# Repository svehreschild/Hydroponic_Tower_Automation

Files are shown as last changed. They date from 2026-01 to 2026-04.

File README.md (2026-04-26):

# Hydroponic_Tower_Automation
Hier finden Sie eine detaillierte Anleitung, um einen modularen Hydroponikturm zu automatisieren. Die Anleitung enthält einen Schaltplan, den Code der Software, eine Liste der benötigten Materialien und eine Schritt-für-Schritt-Anleitung.

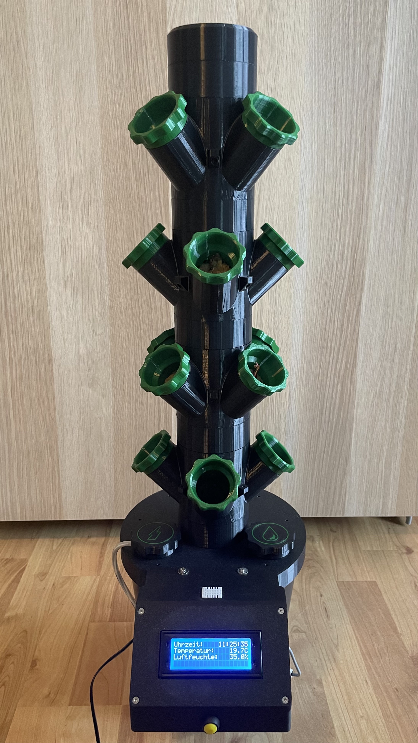
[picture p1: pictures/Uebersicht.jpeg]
Bild-Übersicht


## 3D-Druck
**Grundaufbau:** 
Zunächst werden die benötigten, modularen Komponenten für den Hydroponikturm mit einem 3D-Drucker gedruckt. Als Basis für unser Projekt haben wir die Designs von Luitzor verwendet, die unter der folgenden URL verfügbar sind: [Luitzor's Hydroponic Tower Designs](https://www.thingiverse.com/thing:5712775). Wir empfehlen, diese Designs als Ausgangspunkt zu verwenden, da sie bereits sehr gut durchdacht, modular und funktional erweiterbar sind.

Wir haben die Designs auf 75 % der Originalgröße skaliert, da wir in unserem Fall einen kleineren Turm automatisieren wollten, der auch auf einem Schreibtisch, einer Fensterbank oder ähnlichen begrenzten Flächen Platz findet. Damit das Druckergebnis optimal wird, empfehlen wir die folgenden Druckeinstellungen:

- Material: Extrudr PET-G (lebensmittelecht)
- Drucker: Bambu Lab X1C 
- 0.16mm Optimal @BBL X1C mit folgenden Anpassungen:
    - Fülldichte: 25 % (Gyroid)

Mindestens sollten die folgenden Komponenten gedruckt werden:
- 1x 4-Way_Planting_Module_Hollow_Twist.STL
- 4x Standard_Pot_02_For_4-5-Way_Planting_Module.STL
- 1x Module_Spacer_40mm.STL
- 1x Dispenser_Module_Internal.STL
- 1x IKEA_Muskot_24cm_Lid.STL
- 1x Lid_Without_Holes.STL
- 1x Pump_Cap.STL
- 1x Pump_Cap_Symbol.STL
- 1x Filling_Cap.STL
- 1x Filling_Cap_Symbol.STL

Soll der Turm mehrere Ebenen haben, müssten Sie pro Ebene einmal `4-Way_Planting_Module_Hollow_Twist.STL`, viermal `Standard_Pot_02_For_4-5-Way_Planting_Module.STL` und einmal `Module_Spacer_40mm.STL` drucken. Der Abstandhalter `Module_Spacer_40mm.STL` ist nicht zwingend notwendig, aber wir empfehlen ihn, um den Pflanzen mehr Platz zum Wachsen zu geben. Außerdem empfehlen wir, mehrere Pflanzenpods `Standard_Pot_02_For_4-5-Way_Planting_Module.STL`, als Reserve zu drucken, falls eine Pflanze nicht gedeiht oder ersetzt werden muss.

Bei der Kombination der Abdeckkappen und der zugehörigen Symbole empfehlen wir, die Symbole mit einem Kleber auf die Kappen zu kleben oder, mit einem Drucker, der über ein AMS (Automatisches Materialwechselsystem) verfügt, die Symbole in einer anderen Farbe zu drucken, um eine bessere Sichtbarkeit zu gewährleisten.

Gedruckte Symbole in Abdeckkappen

**Unsere 3D Files**:
Zur sicheren Unterbringung der Elektronik, haben wir ein Gehäuse und Platinenhalterungen designed. Diese Dateien finden Sie im Ordner `3D_Designs`. Sie benötigen die folgenden Dateien jeweils einmal:
- Vertical_Gardening_Housing.stl
- Vertical_Gardening_Housing_Lid.stl
- Sockelhalter_Platine_Main.stl
- Sockelhalter_Relais.stl

**Kalkulation:** 
In der Datei `3D_Berechnung.xlsx` können Sie vorab kalkulieren, wie viel Filament für den Druck der benötigten Komponenten in Abhängigkeit zur Anzahl der Etagen und zu den empfohlenen Einstellungen gebraucht wird.

**Informationen zum Filament:**
Bei dem verwendeten Filament handelt es sich um lebensmittelechtes PET-G von Extrudr. Weitere Informationen zum Filament finden Sie hier in dem `Regulatorischen Datenblatt`: [Extrudr PET-G](https://www.extrudr.com/de/de/products/petg/).

Es sei noch darauf hingewiesen, dass PET-G im Vergleich zu PLA eine höhere Drucktemperatur benötigt und die Druckbetttemperatur ebenfalls höher eingestellt werden muss.

Anstelle des PET-G der Firma Extrudr kann auch anderes, lebensmittelechtes PET-G Filament verwendet werden. Es sollte jedoch auf entsprechende Zertifikate und Angaben des Herstellers geachtet werden, um sicherzustellen, dass das Filament für den Kontakt mit Lebensmitteln geeignet ist. 

Falls Sie sich mit dem Thema lebensmittelechtes Filament näher beschäftigen möchten, finden Sie hier einige weitere Informationen: 
- [Leitfaden für den lebensmittelechten 3D-Druck](https://formlabs.com/de/blog/leitfaden-lebensmittelechtheit-3d-druck/)
- [FDA-Bestimmungen, CFR 21](https://www.accessdata.fda.gov/scripts/cdrh/cfdocs/cfcfr/CFRSearch.cfm)
- [EU-Richtlinien 10/2011](https://eur-lex.europa.eu/legal-content/EN/ALL/?uri=CELEX%3A32011R0010)

## Elektronik
Die Automatisierung des Hydroponikturms umfasst die Erstellung einer Steuerplatine, die folgende Komponenten beinhaltet:

- Arduino Nano
- Display mit I2C Schnittstelle
- DHT22 Sensor (für Temperatur und Luftfeuchtigkeit)
- Schwimmerschalter (Wasserstandserkennung)
- Buck-Converter
- Relaismodul
- Pumpe
- RTC Modul

Eine detaillierte Stückliste mit Vorschlägen zu Anbietern ist in der Datei `Bauteilliste.xlsx` enthalten.

In der Bauteilliste ist auch eine Blanko-Platine aufgeführt. Wir haben im Rahmen unseres Projektes eine Lochrasterplatine entworfen, auf der die benötigten Komponenten verlötet wurden. Es steht Ihnen jedoch frei, ob Sie eine eigene Platine entwerfen oder eine Lochrasterplatine verwenden möchten.

Wir empfehlen die Erstellung einer Platine mit den Maßen (120 mm, 40 mm) um diese optimal in die vorgesehene 3D-gedruckte Halterung einzusetzen.

Sie benötigen außerdem noch folgendes Zubehör:
- Lötstation
- Lötzinn
- Schrumpfschlauch
- Kabelbinder
- Kabel

Anhand des [Schaltplans](Schaltplan.pdf) können Sie die Verdrahtung der einzelnen Komponenten nachvollziehen:
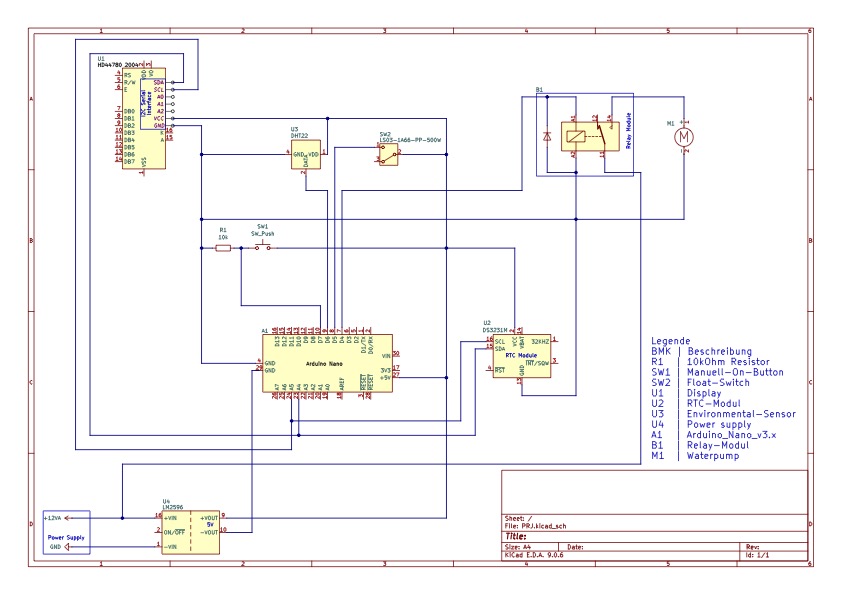
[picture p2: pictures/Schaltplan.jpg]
Schaltplan


## Zusätzliches Zubehör
Um dem Hydroponikturm eine stabile und wasserdichte Basis zu geben, empfehlen wir die Verwendung eines passenden Topfs. In unserem Fall haben wir (anders als im Originaldesign von Luitzor) einen entsprechenden Topf im Baumarkt mit einem Außendurchmesser von 21,5cm gekauft, der sich mit einem gekauften Dichtungsband für Fenster und Türen, welches in den Deckel eingeklebt wird, abdichten lässt.
Der (auf 75% skalierte) Deckel hat einen Innendurchmesser von ca. 22cm, daher sollte der Topf einen Außendurchmesser haben, der etwas kleiner ist, damit der Deckel passt.

Deckel

## Software
Der Quellcode für die Steuerung des Hydroponikturms ist in der Datei `Hydroponic_Tower_Automation.ino` enthalten. 

Die Software ist so konzipiert, dass sie die folgenden Funktionen erfüllt:
- Speicherung und Abruf von Einstellungen über das RTC-Modul
- Anzeige von Temperatur, Luftfeuchtigkeit und Systemstatus auf dem Display
- Displayanzeige der verbleibenden Laufzeit der Pumpe oder der restliche Pausenzeit
- Pausenfunktion: Durch Drücken des Tasters für 3 Sekunden wird eine 3-stündige Bewässerungspause aktiviert. Ein kurzer Druck während der Pause bricht diese vorzeitig ab
- Steuerung der Pumpe basierend auf manuellen Eingaben und voreingestellten Zeitintervallen
- Alarmierung bei zu niedrigem Wasserstand und Verhindern des Pumpenbetriebs in diesem Fall

Sollten Sie andere Zeitintervalle, Bewässerungsdauern oder zusätzliche Funktionen benötigen, können Sie den Quellcode entsprechend anpassen.

Damit der Code kompiliert werden kann, benötigen Sie die folgenden Bibliotheken, die Sie über den Bibliotheksverwalter der Arduino IDE installieren können:
- RTClib von Adafruit (bei uns Version 2.1.4)
- LiquidCrystal_I2C von Martin Kubovčík, Frank de Brabander (bei uns Version 2.0.0)
- DHT sensor library von Adafruit (bei uns Version 1.4.6)

Spielen Sie den Code auf Ihren Arduino Nano, während Sie die Verdrahtung mit dem RTC-Modul gemäß dem Schaltplan verbunden haben, um die Uhrzeit einmalig einzustellen. Nach dem Schreiben der aktuellen Uhrzeit auf das RTC-Modul können Sie diesen Codeblock erneut auskommentieren, um die Uhrzeit nicht bei jedem Neustart zu überschreiben. Sobald die Uhrzeit eingestellt ist, ist das RTC-Modul in der Lage, die Zeit auch bei einem Stromausfall (der Hauptspannungsversorgung) zu behalten, da es über eine Knopfzellenbatterie weiterhin versorgt wird.

## Montage
Beginnen Sie mit dem Zusammenbau der 3D-gedruckten Komponenten gemäß der Anleitung von [Luitzor](https://www.thingiverse.com/thing:5712775). Dies sollte sehr intuitiv sein. 

Bauen Sie jeweils eine Baugruppe aus einem 4-Wege-Pflanzenmodul, vier Pflanzenpods und einem Abstandhalter zusammen. Wiederholen Sie diesen Schritt für die gewünschte Anzahl an Etagen. Nun beginnen Sie mit dem Dispenser-Modul, an das nun der Wasserschlauch angeschlossen wird.

Foto Dispenser-Modul mit Schlauch

Im Anschluss nehmen Sie die zuvor erstellten Baugruppen und stapeln diese auf das Dispenser-Modul. Der Wasserschlauch wird durch die runden Ausschnitte in allen Modulen hindurchgeführt.  

Modulgruppe mit Schlauch1

Modulgruppe mit Schlauch2

Achten Sie darauf, dass die Module korrekt ausgerichtet sind, damit die Pflanzenpods später nicht direkt untereinander, sondern um 45 Grad versetzt, eingesetzt werden können.

Modulgruppen um 45 Grad versetzt

Der Deckel des Topfs wird ebenfalls bestückt mit den Abdeckungen für die Pumpe und dem Zugang zum Wassertank. In der Mitte des Deckels wird der Turm aufgeschraubt.

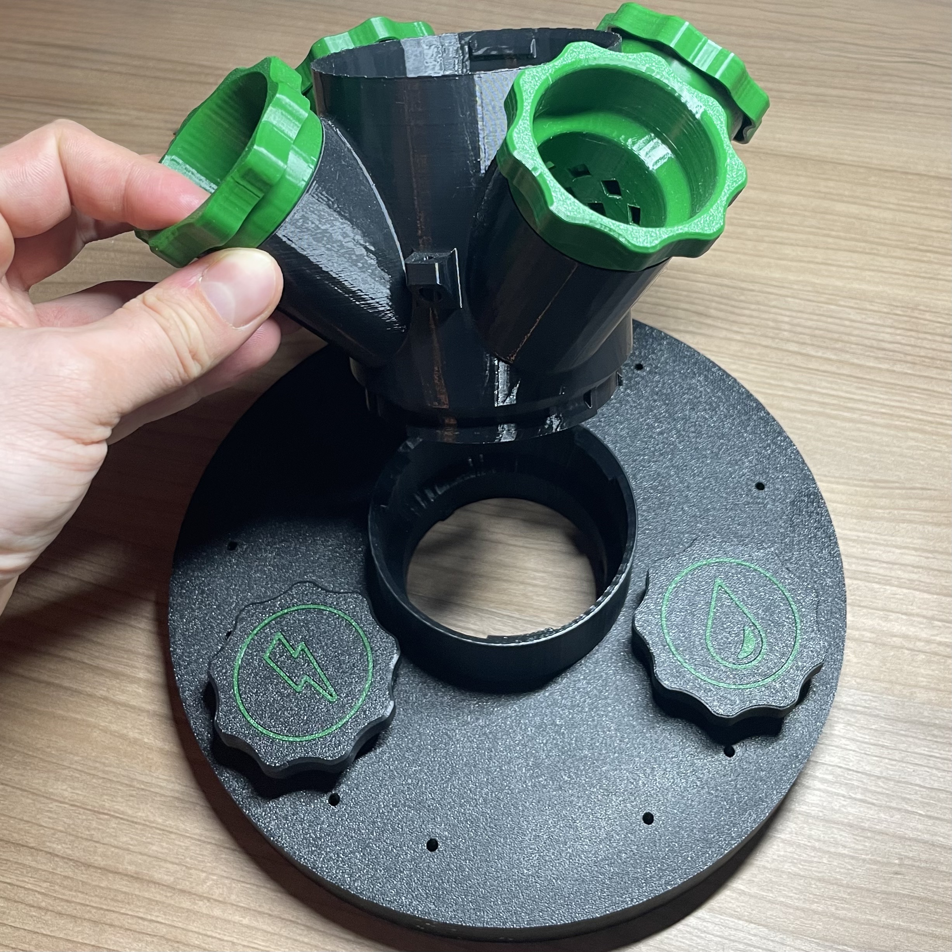
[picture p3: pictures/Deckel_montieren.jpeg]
Bestückung des Deckels


In den Topf wird ein entsprechendes Loch für den Schwimmerschalter gebohrt, der dann von außen in den Topf eingesetzt und mit einer Mutter befestigt wird. Achten Sie darauf, dass der Sensor wasserdicht im Topf sitzt, damit kein Wasser austreten kann.

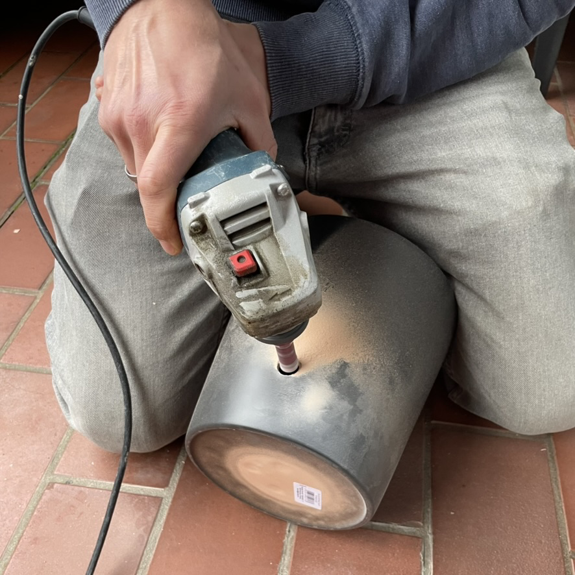
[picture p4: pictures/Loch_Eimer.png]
Loch im Topf


Anschließend erhitzen Sie vier M3 Einschmelzgewinde (mit einer Länge von ca. 6 mm) und setzen diese in das Gehäuse zur Befestigung des Deckels ein.

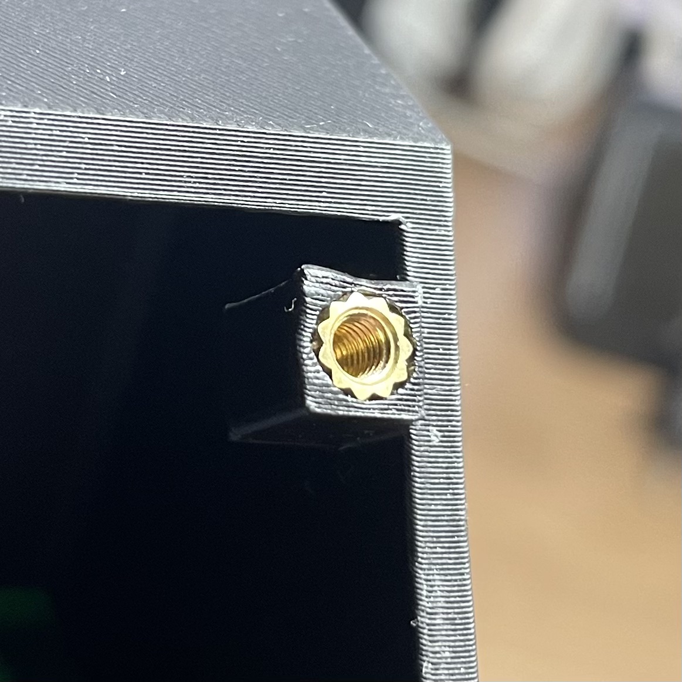
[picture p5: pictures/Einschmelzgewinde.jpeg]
Einschmelzgewinde


Außerdem verkleben Sie die Hauptplatinenhalterung und den DHT22 im Gehäuse mit einem geeigneten Kleber (z. B. Zweikomponentenkleber).
Achten Sie darauf, die Platinenhalterung so zu positionieren, dass der Anschluss für die Spannungsversorgung der Platine durch die Aussparung im Gehäuse passt.

Die Platinenhalterung für das Relaismodul wird lediglich mit zwei M2,5 Schrauben (Länge maximal 4,5 mm) befestigt. Das RTC-Modul wird in dem Gehäuse an dem dafür vorgesehenen Platz mit drei M2,5 Schrauben (Länge maximal 6 mm) angebracht. 
Beachten Sie, dass zu lange Schrauben das Gehäuse beschädigen können.
Den Taster zum Aktivieren des manuellen Pumpenbetriebs können Sie an der Vorderseite des Gehäuses in dem entsprechenden Ausschnitt anbringen und ihn mit der mitgelieferten Mutter befestigen.

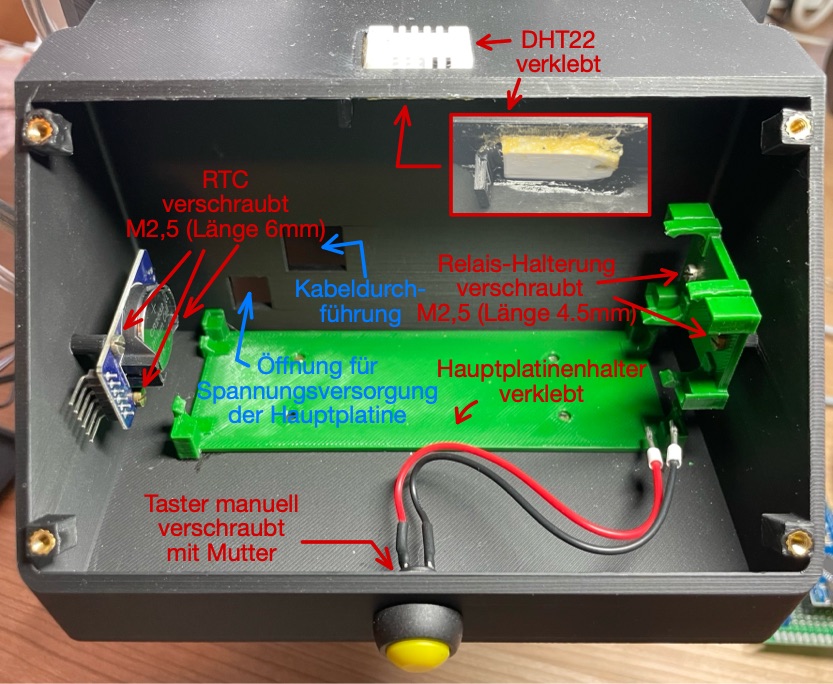
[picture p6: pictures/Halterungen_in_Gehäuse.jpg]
Gehäuse mit Komponenten und Beschriftungen


In den Deckel des Gehäuses wird das Display mit vier M2,5 Schrauben (Länge maximal 4,5 mm) befestigt.
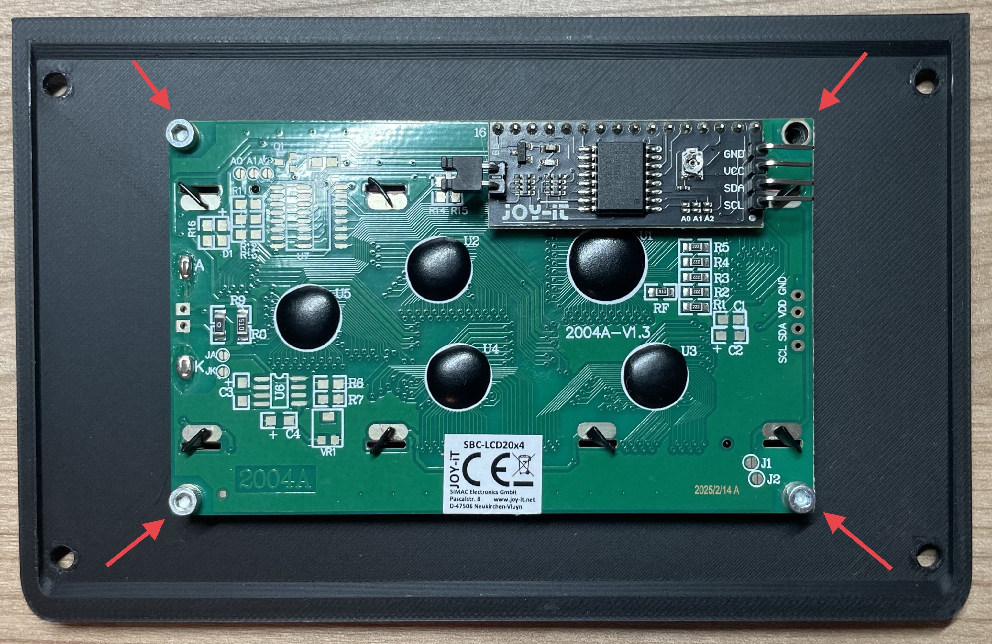
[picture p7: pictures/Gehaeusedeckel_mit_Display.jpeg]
Gehäusedeckel mit Display


Im Anschluss verlöten Sie die Elektronikkomponenten, die auf der Hautplatine Platz finden sollen gemäß dem [Schaltplan](Schaltplan.pdf).
Sinnvoll ist es die Verbindungen zu den einzelnen externen Komponenten über Schraubverbindungen herzustellen, damit diese bei Bedarf einfach getauscht werden können. 

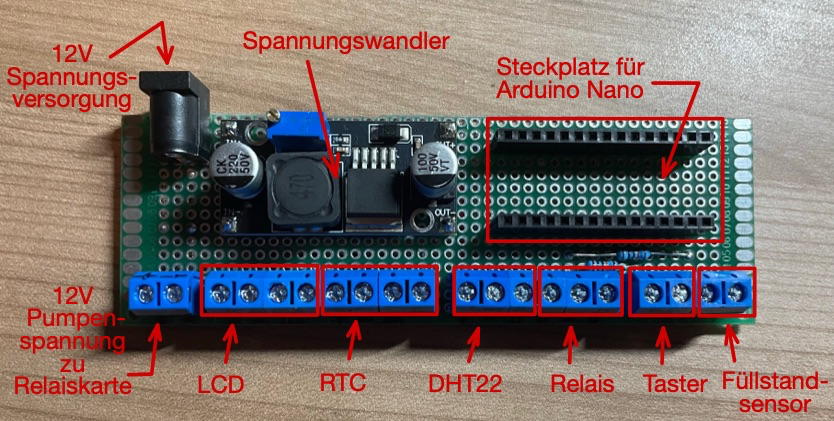
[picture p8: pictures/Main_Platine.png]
Hauptplatine


Die Verkabelung der einzelnen Komponenten im Gehäuse erfolgt ebenfalls gemäß dem [Schaltplan](Schaltplan.pdf). Achten Sie darauf, dass die Kabel ausreichend lang sind, um alle Komponenten zu erreichen. Sinnvoll ist es, die Kabel mit Schrumpfschlauch zu isolieren und entsprechende Aderendhülsen zu verwenden.

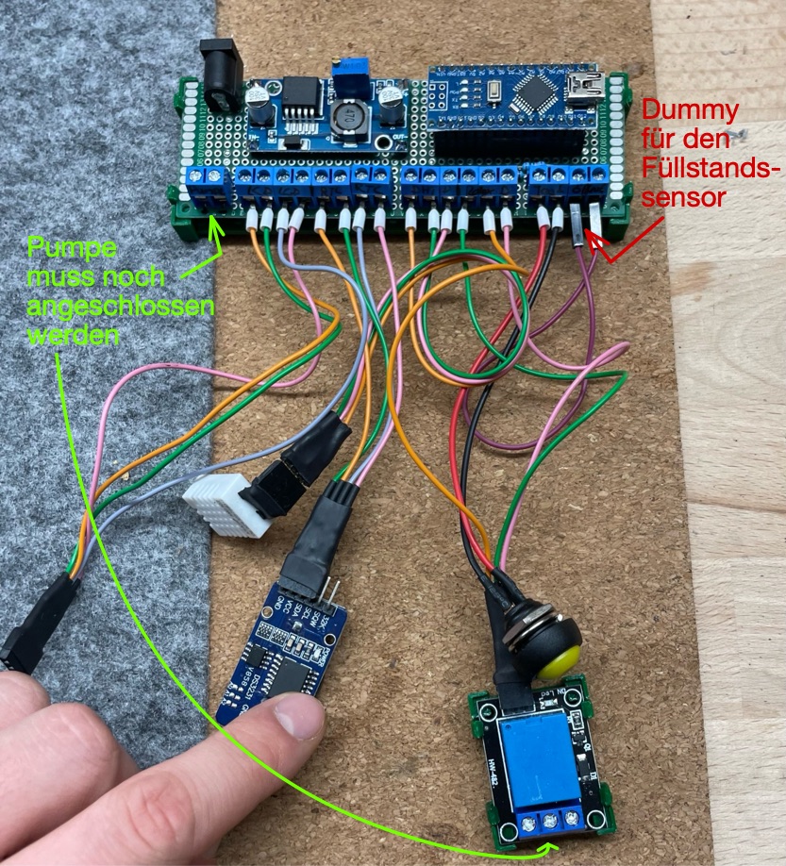
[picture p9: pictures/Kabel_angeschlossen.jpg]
Hauptplatine mit Verkabelung


Bevor die Pumpe in den Topf eingesetzt wird, wird sie mit einem Stück Fliegengitter vor Verunreinigungen geschützt. Das Fliegengitter wird mit einem Kabelbinder an der Pumpe befestigt. 

Pumpe mit Fliegengitter

Anschließend wird die Pumpe durch den dafür vorgesehenen Ausschnitt im Deckel des Topfs eingesetzt und mit der Platine entsprechend des Schaltplans verbunden. Das Kabel der Pumpe sollte durch die Aussparung an der Rückseite des Gehäuses geführt werden, damit dieses später geschlossen werden kann.

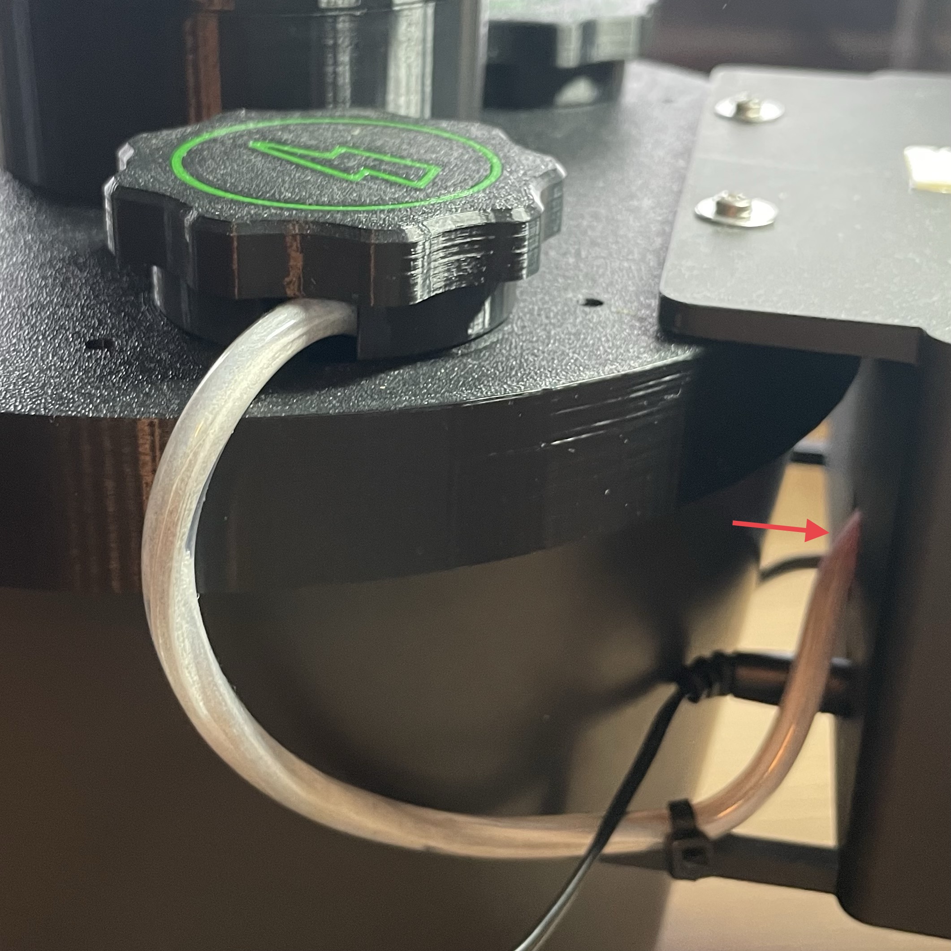
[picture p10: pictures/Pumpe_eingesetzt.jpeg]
Pumpe eingesetzt


Im Anschluss wird nun der finale Feinschliff der Verkabelung durchgeführt. Die Kabel sollten so verlegt werden, dass sie nicht im Weg sind und anschließend vorsichtig mit Kabelbindern fixiert und gebündelt werden. 
Sie können überschüssige Kabellängen kürzen oder aufrollen, um eine ordentliche Verkabelung zu gewährleisten.
Achten Sie darauf, dass Sie keine Kabel quetschen, wenn Sie die Kabelbinder fest ziehen.

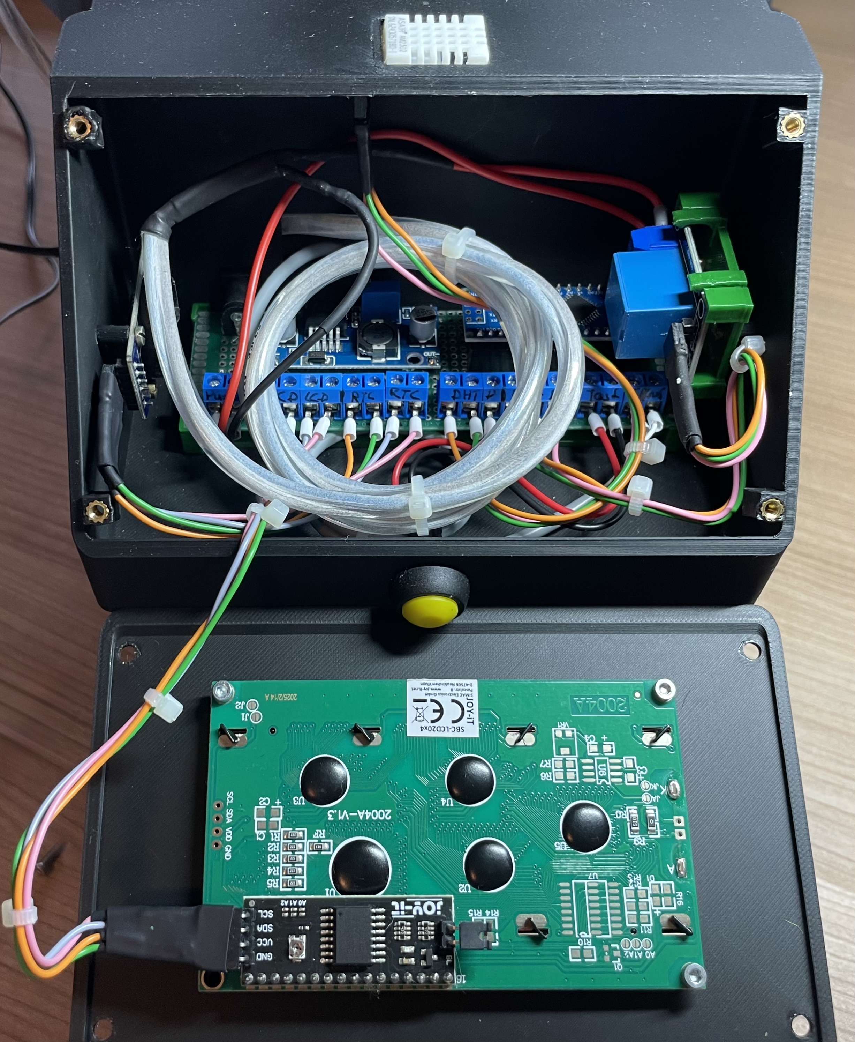
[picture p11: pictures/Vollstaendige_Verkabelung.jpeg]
Vollständige Verkabelung


Nun können Sie das Elektronikgehäuse mit vier M3 Senkkopfschrauben (empfohlene Länge 10 mm) verschließen (Deckel und Gehäuse verbinden).
Achten Sie darauf, dass keine Kabel gequetscht werden, wenn das Gehäuse geschlossen wird.

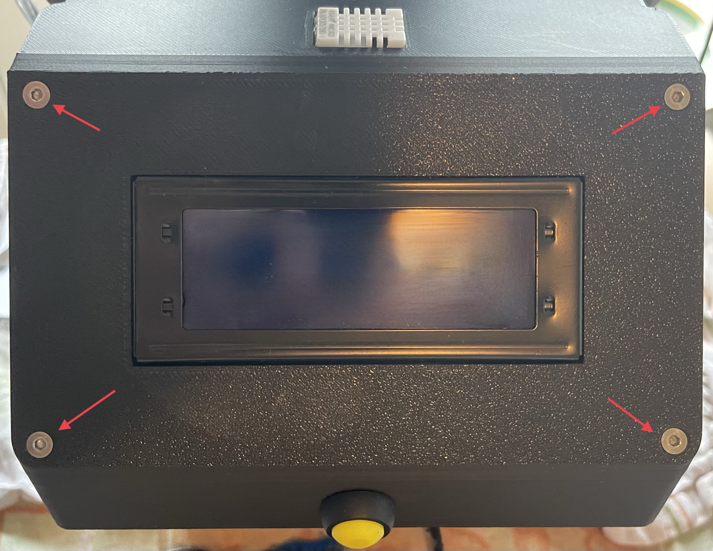
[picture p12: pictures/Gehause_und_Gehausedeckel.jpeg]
Gehäuse und Gehäusedeckel


Im Anschluss wird das verschlossene Gehäuse auf dem Topfdeckel mit zwei M3 Schrauben (empfohlene Länge 15 mm), sowie zwei (oder vier) M3 Muttern befestigt. Verwenden Sie dazu die Langlöcher des Gehäuses und die Löcher im Topfdeckel, die Luitzor für die Befestigung von LED-Trägern vorgesehen hat.

Idealerweise sollten Sie M3 Karosseriescheiben verwenden, um eine bessere Lastverteilung auf den Langlöchern des Gehäuses zu gewährleisten und bei der Befestigung zwei weitere Muttern verwenden und diese gegeneinander festzuziehen, um ein Lösen der Schrauben zu verhindern.

Sicht von oben:
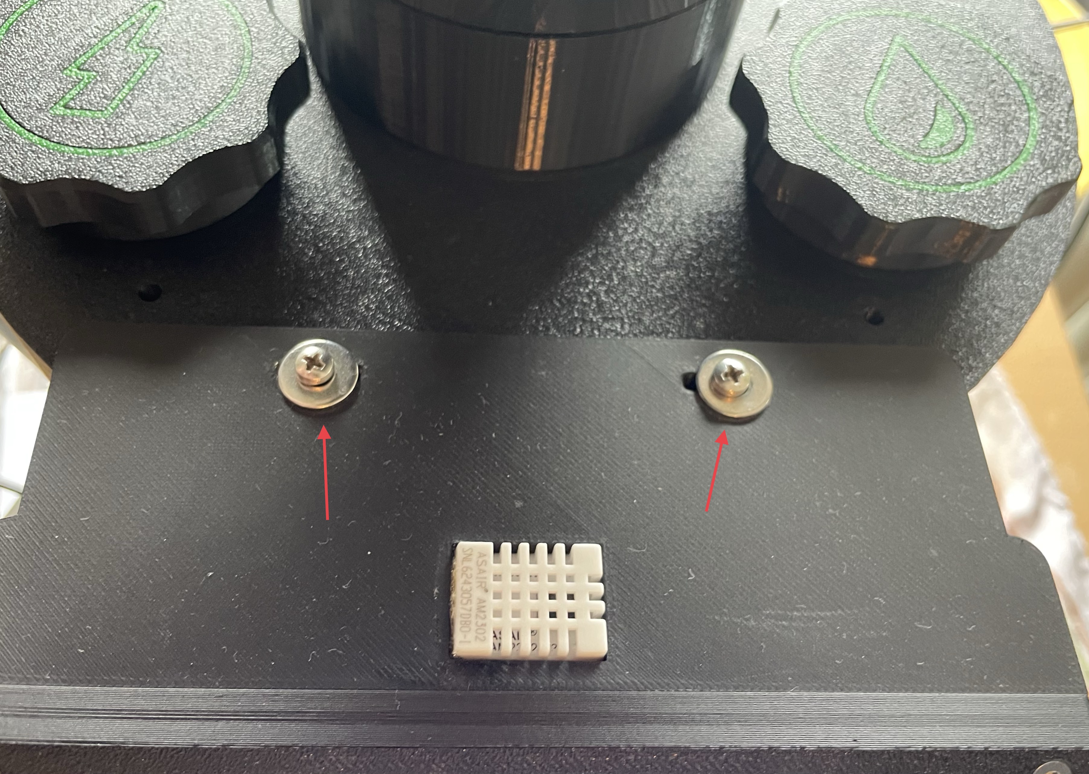
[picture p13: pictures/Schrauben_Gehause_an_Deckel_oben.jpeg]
verschlossenes Gehäuse auf Topf, Sicht von Oben

Sicht von unten:
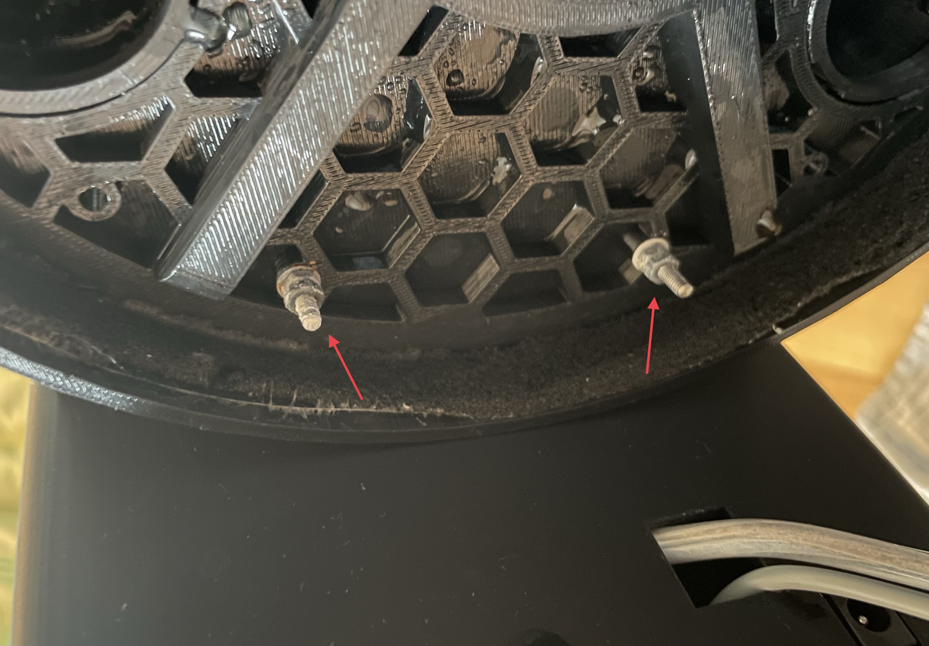
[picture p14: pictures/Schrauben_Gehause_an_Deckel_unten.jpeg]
verschlossenes Gehäuse auf Topf, Sicht von Unten


Achten Sie darauf, dass Sie für die Schrauben und Muttern Edelstahl oder verzinkte Alternativen verwenden, um Korrosion durch die Nähe zum Wasser zu vermeiden.

## Anzüchten von Pflanzen
Im Verlauf unseres Projekts haben wir verschiedene Varianten der Pflanzenanzucht ausgetestet. Im Folgenden beschreiben wir zwei Möglichkeiten, wie Sie die Pflanzen für den Hydroponikturm ziehen können.

Allgemein wird zwischen Licht- und Dunkelkeimern unterschieden. Dementsprechend sollten Sie sich vorab informieren, ob die von Ihnen gewünschten Pflanzen Licht- oder Dunkelkeimer sind, um die Keimbedingungen entsprechend anzupassen.

Eine Möglichkeit ist es, die Samen in feuchtem Küchenpapier oder Watte anzuzüchten. Legen Sie die Samen dazu zwischen zwei feuchte Lagen und halten Sie diese stets feucht. Achten Sie darauf, dass die Samen nicht zu nass liegen, da sie sonst faulen können. Stellen Sie die Samen an einen warmen Ort mit ausreichend Licht (je nach Keimertyp) und warten Sie, bis die Samen keimen. 
Beachten Sie außerdem, dass es je nach Pflanze unterschiedlich lange dauern kann, bis die Samen keimen.

Keimlinge im Küchenpapier

Nach dem Keimen können die kleinen Pflanzen vorsichtig in befeuchtete Steinwollwürfel gepflanzt werden. Diese werden zuvor in die Pods des Hydroponikturms eingesetzt. Achten Sie dabei darauf, die Wurzeln nicht zu beschädigen. 

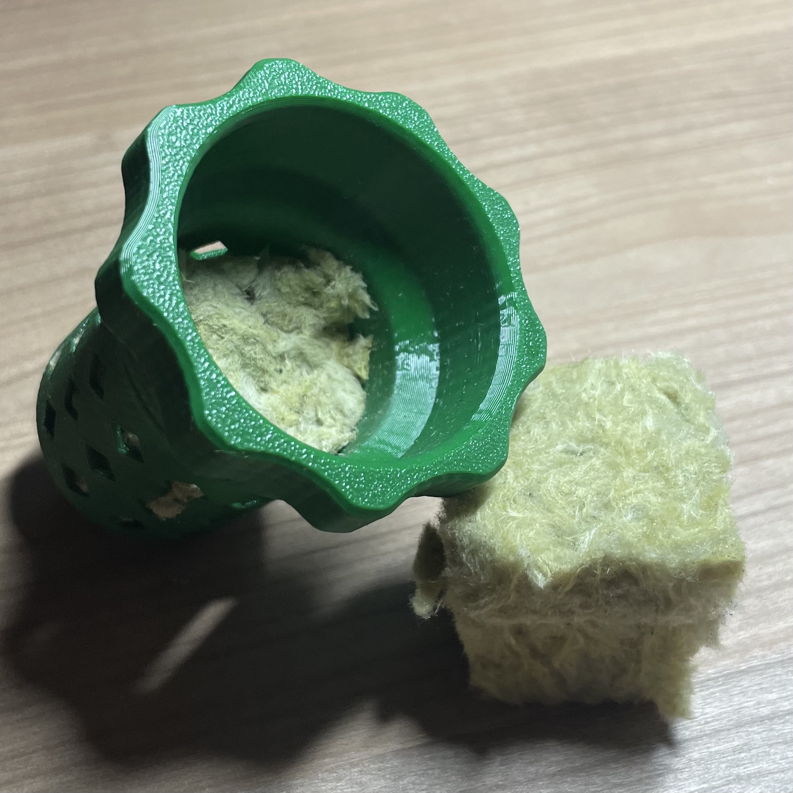
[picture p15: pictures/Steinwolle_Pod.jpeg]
Steinwolle und Pods


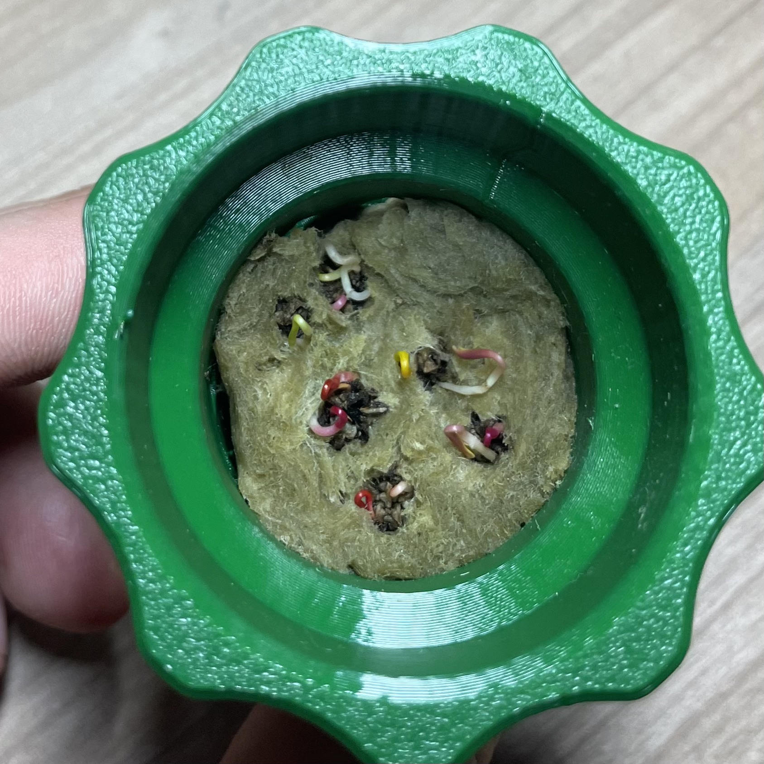
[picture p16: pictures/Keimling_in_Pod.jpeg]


Eine weitere Möglichkeit ist die Anzucht der Pflanzen direkt in den (herausgenommenen) Pods des Hydroponikturms. Füllen Sie die Pods dazu mit feuchter Steinwolle und pflanzen Sie die Samen direkt hinein. Halten Sie das Substrat stets feucht, aber nicht zu nass, und stellen Sie die Pods an einen warmen Ort mit ausreichend Licht (je nach Keimertyp).

Beachten Sie außerdem, dass einige Pflanzen spezielle Anforderungen an die Nährlösungen, den pH-Wert des Wassers und die Lichteinstrahlung haben. Informieren Sie sich daher vorab über die Bedürfnisse der von Ihnen gewünschten Pflanzen, um optimale Wachstumsbedingungen zu gewährleisten.

----
Alternativ können wir empfehlen, die Pflanzen direkt in den Hydroponikturm zu ziehen, indem Sie die Samen in ein kleines Stück feuchter Steinwolle pflanzen, das in die Pods umrandet von Blähton gelegt wird. Auf diese Weise ist die Wahrscheinlichkeit für Wurzelfäule geringer, da die Samen nicht zu nass liegen.

## Inbetriebnahme
Schließen Sie die Stromversorgung an das Gehäuse an. Das Display sollte nun aufleuchten und die aktuellen Messwerte anzeigen, sowie eine Meldung, dass der Wasserstand zu gering ist.

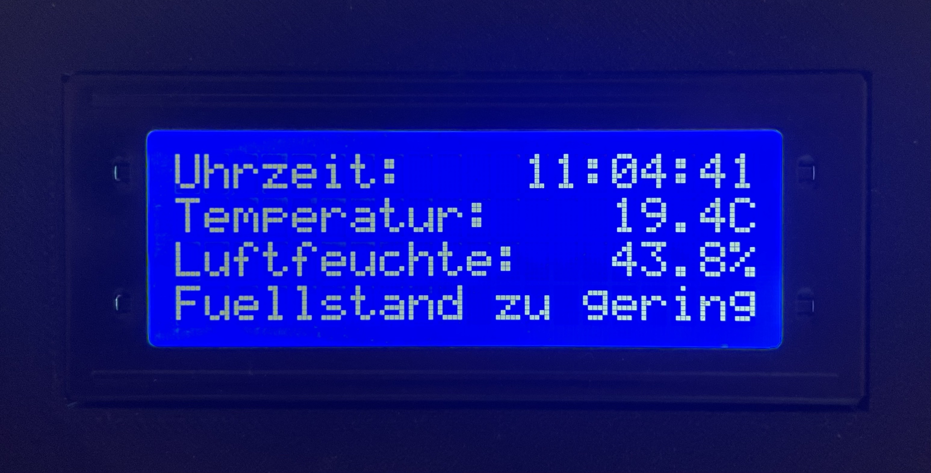
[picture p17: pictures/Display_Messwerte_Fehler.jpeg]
Display mit Messwerten und Fehlermeldung


Füllen Sie den Topf mit Wasser und ggf. einer Nährstofflösung auf. Die Wasserstandsanzeige auf dem Display sollte sich entsprechend aktualisieren.

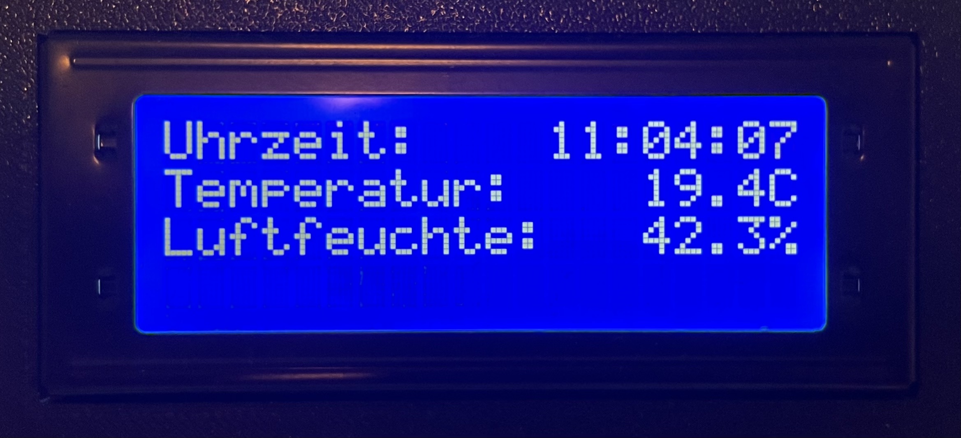
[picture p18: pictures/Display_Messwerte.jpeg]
Display mit Messwerten ohne Fehlermeldung


Stellen Sie sicher, dass die Pumpe korrekt mit dem Wasserschlauch verbunden ist, der in den Hydroponikturm führt, und der Turm keinerlei Undichtigkeiten aufweist.
Drücken Sie den Taster, um die Pumpe manuell zu starten, und überprüfen Sie, ob die Pumpe ordnungsgemäß funktioniert und Wasser durch den Hydroponikturm pumpt, welches von oben nach unten tropfen sollte.

Sollten Sie Probleme mit Undichtigkeiten der Bajonettverbindungen der Module haben, können Sie diese mit einem geeigneten Teflonband abdichten.

Ist die Funktionstüchtigkeit und Dichtigkeit des Systems bestätigt, so können Sie die ersten Pflanzen in den Hydroponikturm einsetzen oder dort anziehen.

Ihr neues, automatisiertes Hydroponiksystem ist nun betriebsbereit! Wir wünschen Ihnen viel Erfolg und Freude beim Anbau Ihrer Pflanzen.

## Warnungen
- Achten Sie darauf, dass alle elektronischen Komponenten vor Wasser geschützt sind, um Kurzschlüsse zu vermeiden.
- Verwenden Sie nur lebensmittelechte Materialien für alle Teile, die mit Wasser und Pflanzen in Kontakt kommen.
- Stellen Sie sicher, dass die Pumpe für den Dauerbetrieb geeignet ist und nicht überhitzt.
- Führen sie nur Arbeiten durch, die Sie sicher beherrschen und die Sie durchführen dürfen. Andernfalls ziehen Sie einen Fachmann hinzu.

## Anregungen 
Im Folgenden haben wir Ihnen einige Ideen zusammengestellt, wie Sie das Projekt erweitern oder anpassen können:
- Integration eines pH- und EC-Sensors zur Überwachung der Nährlösung
- Automatische Auffüllung des Wassertanks bei niedrigem Wasserstand
- Automatisierte Nachfüllung der Nährlösung in den Topf
- Steuerung der Beleuchtung für optimales Pflanzenwachstum
- Mobile App zur Fernüberwachung und Steuerung des Systems um Parameter, wie die Bewässerungszeit anzupassen (ggf. Verwendung eines WLAN-Moduls oder eines ESP32 statt des Arduino Nano)
- Erweiterung des Systems um eine automatische Belüftung der Pflanzen
- Integration von Kameras zur Überwachung des Pflanzenwachstums
- Anpassung der Bewässerung des Systems basierend auf Feuchtigkeitsmessungen in der Steinwolle
- Datenspeicherung und Analyse der Wachstumsbedingungen zur Optimierung des Pflanzenanbaus
- Pufferung des Betriebs bei Stromausfällen durch eine Batterie

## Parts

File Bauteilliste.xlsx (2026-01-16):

Bauteilliste
Material | Anzahl | Herstellerlink | Preis | Herstellerlink alternativ preiswerter | Preis alternativ
Microcontroller | 1 | https://www.reichelt.de/de/de/shop/produkt/arduino_nano_v3_atmega_328_mini-usb-142943 | 19.7 | https://www.pollin.de/p/joy-it-arduino-nano-v3p-precision-ard-nanov3p-arduino-kompatibel-mit-original-chip-811754 | 10.9
Pumpe (Wasser) | 1 | https://www.conrad.de/de/p/comet-1300-01-00-niedervolt-tauchpumpe-600-l-h-5-5-m-1435461.html | 14.99
Schlauch (Wasser) | 3m | https://www.conrad.de/de/p/hozelock-100-101-147-10-mm-meterware-glasklar-pvc-schlauch-3394330.html | 4.47
Relais | 1 |  |  | https://www.amazon.de/ARCELI-STÜCKE-KY-019-Relaismodul-arduino/dp/B07BVXT1ZK | 5.99
RTC-Module | 1 |  |  | https://www.amazon.de/dp/B01M2B7HQB?ref=ppx_pop_mob_ap_share&th=1 | 6.99
Button | 1 |  |  | https://www.amazon.de/dp/B08JCNHF1H | 9.99
DC-DC-Wandler | 1 |  |  | https://www.amazon.de/Converter-APKLVSR-Spannungsregler-Einstellbares-Abwärtsmodul/dp/B0FPG1GFDJ?__mk_de_DE=ÅMÅŽÕÑ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
Füllstandssensor (Wasser) | 1 | https://www.reichelt.de/de/de/shop/produkt/levelsensor_mit_schwimmer_waagerechter_einbau-27691 | 9.8
Umgebungssensor (Temp & Humi) | 1 | https://www.reichelt.de/de/de/shop/produkt/entwicklerboards_-_temperatur-_feuchtigkeitssensor_dht22-266104 | 7.99
Trägermaterial | 3 | https://www.growland.net/Grodan-Steinwollstartbloecke-4x4cm-15-Stueck?_gl | 11.85 | https://a.co/d/cCIFuJb | 12$
Display | 1 | https://www.az-delivery.de/products/hd44780-2004-lcd-display-bundle-4x20-zeichen-mit-i2c-schnittstelle-gruen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 | 8.99
Netzteil | 1 | https://www.reichelt.de/de/de/shop/produkt/netzteil_36_w_12_v_3_a_dc-stecker_5_5x2_1_mm-387959 | 24.7
Platine Blank | 1

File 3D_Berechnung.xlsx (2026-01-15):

3D Druck Liste
Bauteil | Anzahl | Gewicht pro einzelnes Bauteil (100%) [g] | Gesamtgewicht pro Bauteiltyp [g] | Gesamtgewicht Filamenttyp [g] | Skalierung um Faktor [g]
4-Way_Planting_Module_Hollow_Twist.STL | 4 | 223.86 | 895.44 | 1558.6 | 1168.95 | <-- PETG, lebensmittelecht, schwarz
Dispenser_Module_Internal.STL | 1 | 96.32 | 96.32 | 708.31 | 531.2325 | <-- PETG, lebensmittelecht, grün
Filling_Cap.STL | 1 | 36.64 | 36.64
Filling_Cap_Symbol.STL | 1 | 1.04 | 1.04
IKEA_Muskot_24cm_Lid.STL | 1 | 144.16 | 144.16
Lid_Without_Holes.STL | 1 | 90.03 | 90.03
Module_Spacer_40mm.STL | 4 | 65.04 | 260.16
Pump_Cap.STL | 1 | 35.85 | 35.85
Pump_Cap_Symbol.STL | 1 | 1.19 | 1.19
Standard_Pot_02_For_4-5-Way_Planting_Module.STL | 16 | 44.13 | 706.08
Anzahl Etagen |  | Skalierungsfaktor
4 |  | 0.75

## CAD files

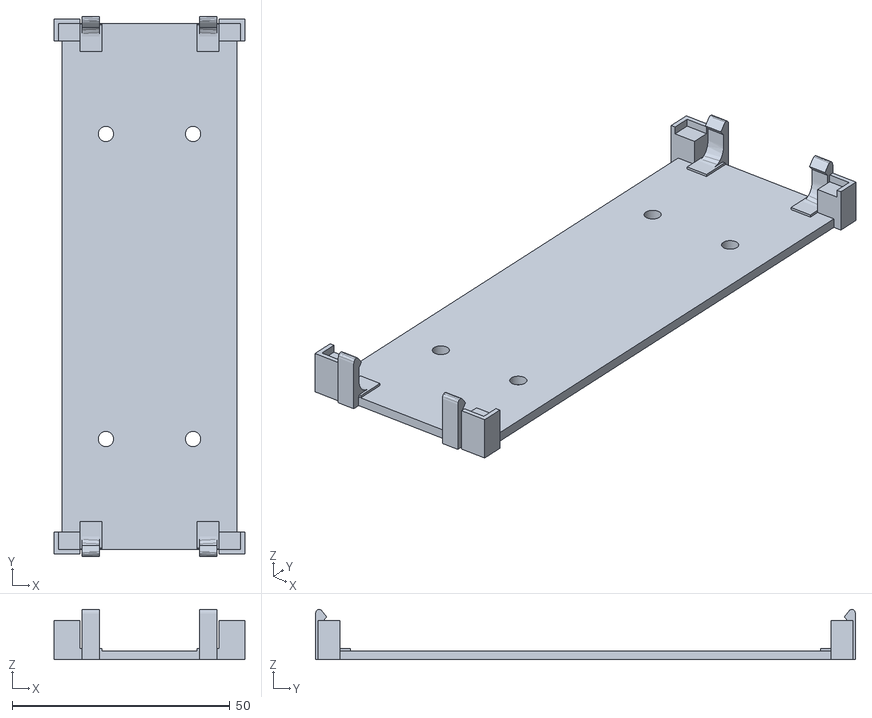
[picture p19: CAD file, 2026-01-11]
3D_Designs/Sockelhalter_Platine_Main.stl.stl
43.8 x 123.9 x 11.5

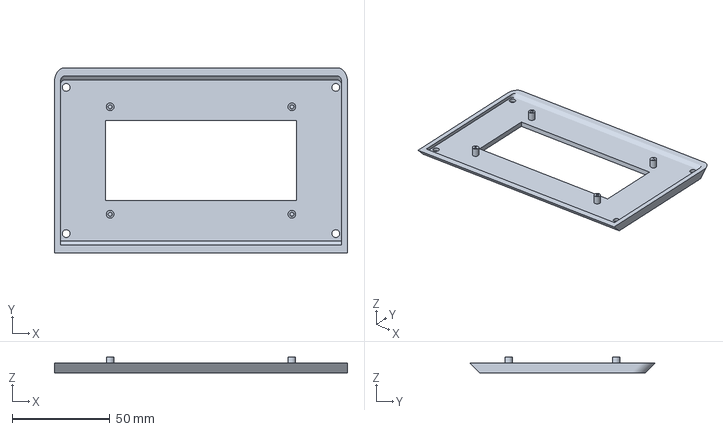
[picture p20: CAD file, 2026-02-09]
3D_Designs/Vertical_Gardening_Housing.3mf
150.0 x 94.9 x 8.00 mm

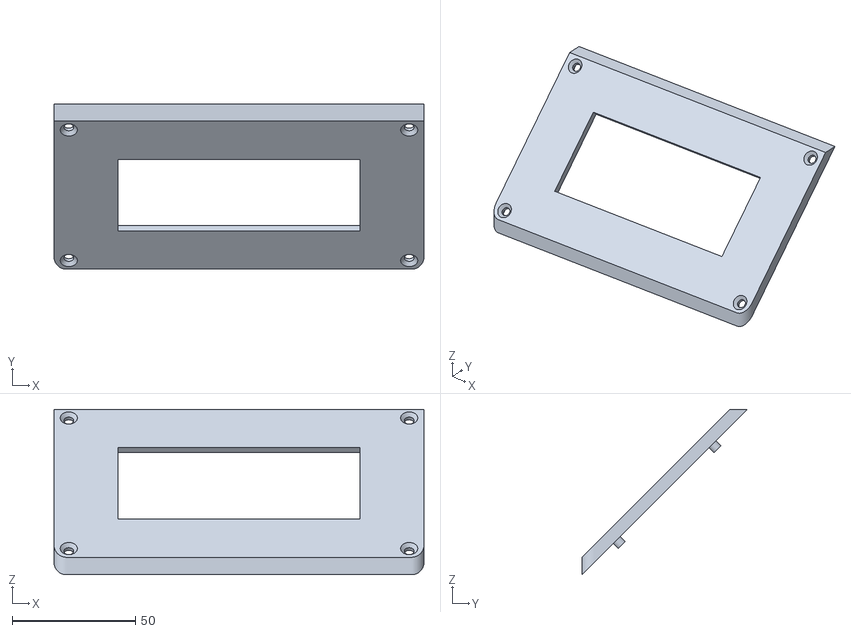
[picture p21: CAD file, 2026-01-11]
3D_Designs/Vertical_Gardening_Housing_Lid.stl
150.0 x 67.1 x 67.1

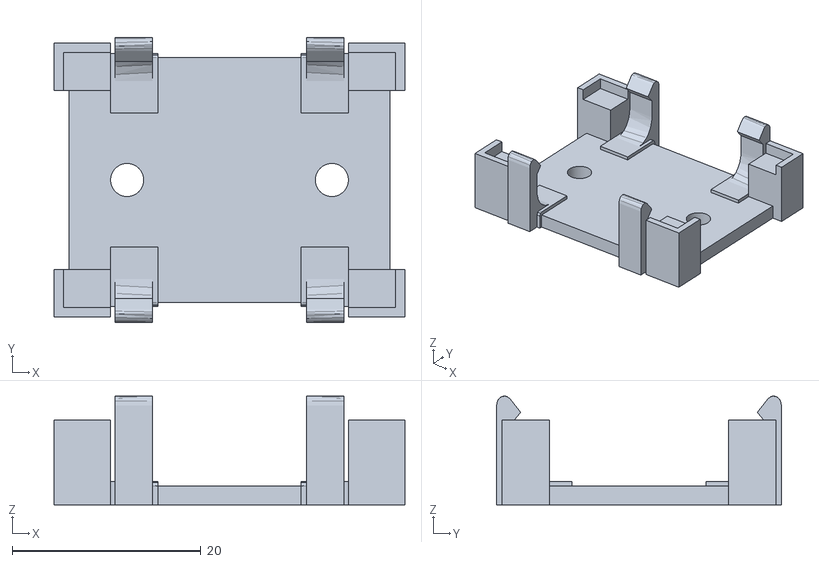
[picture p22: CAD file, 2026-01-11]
3D_Designs/Sockelhalter_Relais.stl
37.2 x 30.2 x 11.5

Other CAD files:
3D_Designs/Vertical_Gardening_Housing.stl

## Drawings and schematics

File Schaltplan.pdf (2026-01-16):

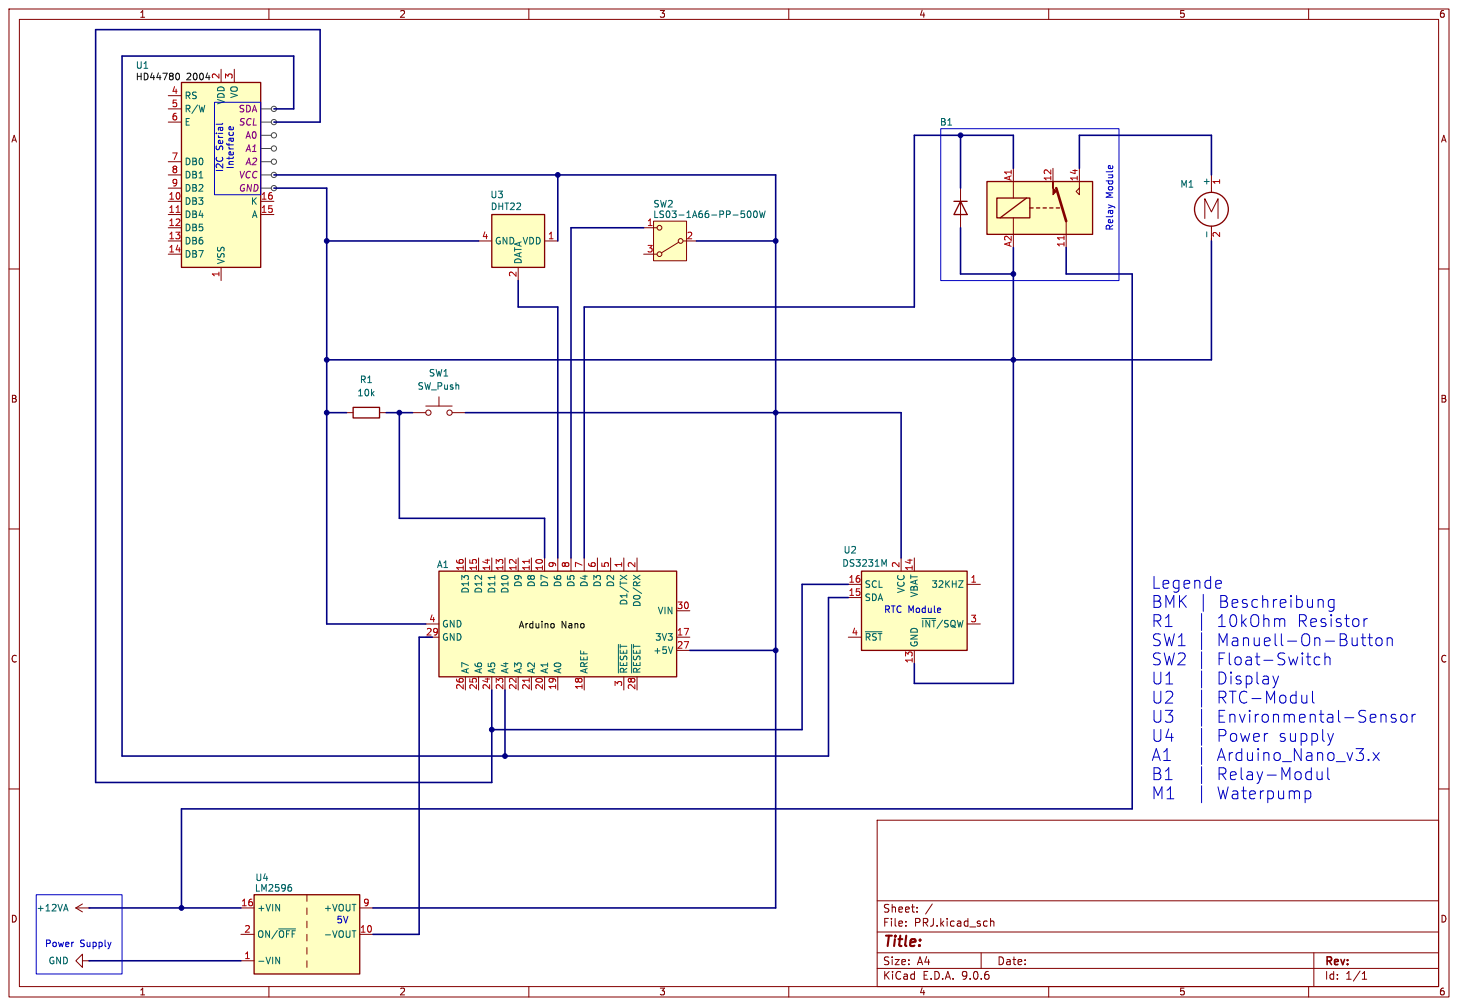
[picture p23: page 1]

Id: 1/1 Title: File: PRJ.kicad_sch Sheet: /

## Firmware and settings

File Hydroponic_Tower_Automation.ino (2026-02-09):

#include <Wire.h>
#include <RTClib.h>
#include <LiquidCrystal_I2C.h>
#include <DHT.h>

RTC_DS3231 rtc;
LiquidCrystal_I2C lcd(0x27,  20, 4);

// PIN Definitionen
#define pumpePin  4    // Pumpe an Pin 4
#define tasterPin 7    // Taster an Pin 7
#define fuellstand 5
#define DHTPIN 6   
#define DHTTYPE DHT22

// Anpassbare Zeiten
const unsigned long DAUER_AUTO    = 30000;   // Bewässerung (Automatik)
const unsigned long DAUER_MANUELL = 10000;    // Bewässerung (Manueller Tastendruck)
const int INTERVALL_MINUTEN       = 30;       // Alle X Minuten gießen
const int START_STUNDE            = 9;        // Ab XX:00 Uhr
const int ENDE_STUNDE             = 20;       // Bis XX:00 Uhr
const unsigned long PAUSE_DAUER   = 3 * 3600000ULL; // X=3 Stunden Pause nach Langdruck (ULL = Unsigned Long Long)
const unsigned long LONG_PRESS_ZEIT = 3000;   // Langdruck

// Variablen
float temp;
float humidity;
unsigned long letzteSerialZeit = 0;
unsigned long pumpeStartZeit = 0;
unsigned long pauseStartZeit = 0;
unsigned long tasterGedruecktZeit = 0;

bool pumpeAn = false;
bool tasterWarGedrueckt = false;

enum PumpenModus { KEINER, AUTO, MANUELL, PAUSE };
PumpenModus pumpenModus = KEINER;

DHT dht(DHTPIN, DHTTYPE);


void setup() {
  Serial.begin(9600); // Serieller Monitor zur Kontrolle
  if (!rtc.begin()) {
    Serial.println("RTC nicht gefunden!"); 
    while (1);
  }

  // Uhrzeit setzen (einmalig)
  // Format: Jahr, Monat, Tag, Stunde, Minute, Sekunde
  // rtc.adjust(DateTime(2026, 2, 9, 18, 21, 40)); 


  pinMode(pumpePin, OUTPUT);
  digitalWrite(pumpePin, LOW);
  
  pinMode(tasterPin, INPUT); // (externer) Pullup, weil Taster gegen GND
  pinMode(fuellstand, INPUT);


  lcd.init();
  lcd.backlight();
  dht.begin();
}

void loop() {
  DateTime jetzt = rtc.now();
  temp = dht.readTemperature();
  humidity = dht.readHumidity();
  unsigned long aktuelleMillis = millis();

  /// TASTER-LOGIK (Kurz/Lang)
  bool tasterStatus = digitalRead(tasterPin);

  if (tasterStatus == HIGH) { // Taster wird gedrückt
    if (!tasterWarGedrueckt) {
      tasterGedruecktZeit = aktuelleMillis;
      tasterWarGedrueckt = true;
    }
    // Langdruck erkannt?
    if (aktuelleMillis - tasterGedruecktZeit >= LONG_PRESS_ZEIT && pumpenModus != PAUSE) {
      pumpeAn = false;
      digitalWrite(pumpePin, LOW);
      pumpenModus = PAUSE;
      pauseStartZeit = aktuelleMillis;
      Serial.println("PAUSE AKTIVIERT");
    }
  } 
  else { // Taster losgelassen
    if (tasterWarGedrueckt) {
      unsigned long drueckDauer = aktuelleMillis - tasterGedruecktZeit;
      
      if (drueckDauer < LONG_PRESS_ZEIT) {
        if (pumpenModus == PAUSE) {
          pumpenModus = KEINER; // Pause abbrechen
          Serial.println("PAUSE ABGEBROCHEN");
        } 
        else if (!pumpeAn && digitalRead(fuellstand) == HIGH) {
          pumpeAn = true;
          pumpenModus = MANUELL;
          pumpeStartZeit = aktuelleMillis;
          digitalWrite(pumpePin, HIGH);
        }
      }
      tasterWarGedrueckt = false;
    }
  }

  // PAUSEN-TIMER
  if (pumpenModus == PAUSE && (aktuelleMillis - pauseStartZeit >= PAUSE_DAUER)) {
    pumpenModus = KEINER;
    Serial.println("PAUSE BEENDET");
  }

  // LCD ANZEIGE (Display Zeilen 1-3)
  lcd.setCursor(0, 0); lcd.print("Uhrzeit:    ");
  if (jetzt.hour() < 10) lcd.print("0"); lcd.print(jetzt.hour()); lcd.print(":");
  if (jetzt.minute() < 10) lcd.print("0"); lcd.print(jetzt.minute()); lcd.print(":");
  if (jetzt.second() < 10) lcd.print("0"); lcd.print(jetzt.second());

  lcd.setCursor(0, 1); lcd.print("Temp:          "); lcd.print(temp, 1); lcd.print("C");
  lcd.setCursor(0, 2); lcd.print("Feuchte:       "); lcd.print(humidity, 1); lcd.print("%");

  // SYSTEM-STEUERUNG (Display Zeile 4)
  
  // Füllstand kritisch
  if (digitalRead(fuellstand) == LOW) {
    pumpeAn = false;
    pumpenModus = KEINER;
    digitalWrite(pumpePin, LOW);
    lcd.setCursor(0, 3);
    lcd.print("Fuellstand zu gering");
  } 
  // Pause aktiv
  else if (pumpenModus == PAUSE) {
    unsigned long rest = (PAUSE_DAUER - (aktuelleMillis - pauseStartZeit)) / 1000;
    int h = rest / 3600;
    int m = (rest % 3600) / 60;

    lcd.setCursor(0, 3);
    lcd.print("Pause:        "); 
    
    lcd.setCursor(13, 3);
    
    // Stunden rechtsbündig (2 Stellen)
    if (h < 10) lcd.print(" "); 
    lcd.print(h);
    lcd.print("h ");

    // Minuten mit führender Null (immer 2 Stellen)
    if (m < 10) lcd.print("0");
    lcd.print(m);
    lcd.print("m");
  }
  // Pumpe läuft (Automatik oder Manuell)
  else if (pumpeAn) {
    unsigned long laufzeit = (pumpenModus == AUTO) ? DAUER_AUTO : DAUER_MANUELL;
    long verbleibend = (laufzeit - (aktuelleMillis - pumpeStartZeit)) / 1000;

    if (verbleibend > 0) {
      lcd.setCursor(0, 3);
      lcd.print(pumpenModus == AUTO ? "Auto-Run: " : "Manu-Run: ");
      
      // Cursor auf Spalte 15 setzen (Platz für bis zu 4 Ziffern + 's')
      lcd.setCursor(15, 3); 

      // Fallunterscheidung für rechtsbündige Ausrichtung
      if (verbleibend < 10) lcd.print("   ");    // 3 Leerzeichen bei 1 Stelle
      else if (verbleibend < 100) lcd.print("  "); // 2 Leerzeichen bei 2 Stellen
      else if (verbleibend < 1000) lcd.print(" "); // 1 Leerzeichen bei 3 Stellen
      
      lcd.print(verbleibend);
      lcd.print("s");
    } else {
      pumpeAn = false;
      pumpenModus = KEINER;
      digitalWrite(pumpePin, LOW);
      lcd.setCursor(0, 3); lcd.print("                    ");
    }
  }
  // Automatik Start-Check
  else if (jetzt.hour() >= START_STUNDE && jetzt.hour() < ENDE_STUNDE && 
           jetzt.minute() % INTERVALL_MINUTEN == 0 && jetzt.second() == 0 && 
           pumpenModus == KEINER) {
    pumpeAn = true;
    pumpenModus = AUTO;
    pumpeStartZeit = aktuelleMillis;
    digitalWrite(pumpePin, HIGH);
  }
  // Standby
  else {
    lcd.setCursor(0, 3);
    lcd.print("Bereit              ");
  }

  delay(100); 
}

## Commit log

2026-01-15 update mit Joshua
    [3D_Berechnung.xlsx, Bauteilliste.xlsx]
2026-02-09 update: Pausenmodus durch Langzeitdruck
    [Vertical_Gardening_Housing.3mf]
2026-02-09 Update: Anpassung der Pausenzeitanzeige
